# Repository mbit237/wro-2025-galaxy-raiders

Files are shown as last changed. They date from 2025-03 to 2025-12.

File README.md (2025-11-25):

# wro-2025-galaxy-raiders -- solution summary

This repository contains the full stack for the robot: electronics (PCB design and fabrication artifacts), sensors (2D LiDAR, gyro, wheel encoders, compass), decision logic (landmark-based localisation and odometry that are fused using a complementary filter), navigation (path planning, proportional steering), colour detection for the Obstacle Challenge (Raspberry Pi Camera–based colour blob detection for green and red), and a set of utilities for calibration, plotting, as well as testing.

It is implemented in Python and designed to run on a Raspberry Pi 4b which is the primary controller. The Pi interfaces directly with the sensors (LiDAR via serial/USB, MPU6050 gyro via I²C, wheel encoders via GPIO), and controls the navigation (continuous DC drive through a motor driver; steering via a PWM-controlled servo). The custom PCB consolidates power distribution, connectors, and signal routing. 

During the run, the program reads initial ranges to estimate the robot’s start pose, continuously merges odometry with landmark corrections, follows the active path, and stops automatically once a path-segment counter reaches the configured limit.

**PCB (wro-pcb-v2 folder)**
Contains everything needed to fabricate and assemble the controller board:
Schematic & PCB: Source files for the custom board (signal routing for power in, motor driver, servo PWM, I²C, UART/USB headers for sensors, encoder inputs).
Drill / CAM: Drill files and drill G-code for CNC milling; SVGs of the board outline and copper to be milled with LaserWeb 
Connected components
Power: Battery input (screw terminal), voltage regulator for motor driver, and servo.
Actuators: Screw terminals/headers to the motor driver output and a 3-pin servo header (GND, +5/6V BEC, PWM).
Sensors: I²C header for MPU6050; UART header for LiDAR; encoder inputs to GPIO connectors.
Tactile button input to GPIO for initialisation 

**Localisation using sensors:**
coind4: functions for current lidar, parsing in each data frame and checking the checksum 
gyro.py (mpu6050): basic functions for gyro to update heading
gyro_calibration_saver.py: saves the gyro calibration readings 
[unused] lds02rr.py: functions for previous lidar, also pareses in each data frame and checks the checksum
[unused] compass.py: functions for compass module to read its heading, not implemented in current version

**Navigation**
spike.py: functions to match to lidar points to landmarks 
estimate_pose.py: functions for odometry, which uses wheel rotation and gyro to estimate the robot's position and heading while it is running. New estimate_pose function uses vectors
drive.py: navigation functions 
step_count: receive signals from encoder to calculate number of steps after a certain period of time 
steering_p: driving servo motor with pwm signal that is derived from the direction in degrees
navigation.py: functions to augment robot’s paths and drive to the path which utilises proportional control to avoid steering off path

**Obstacle Challenge**
Using camera to identify the position of the red and green blocks to know which path to take at each decision point, ie after the turn at each corner
rpicam.py: functions for detection of red and green blobs based on HSV thresholds using opencv
rpicam_calibration.py: tool to calibrate HSV thresholds for different colours with sliders using opencv

**main.py:**
specify the variables and constants: filter ratios for spike and odometry, paths for the different challenges / scenarios 
get the initial position of the robot by checking the distance away from the walls
merging the positions derived from odometry and spike using complementary filter 
while loop that checks whether the path count has reached the limit to stop the programme automatically

**Miscellaneous / Testing**
motor wiring.avif: wiring for the encoder 
button.py: activate the code when button pressed 
Plotting using sockets
client_raspi.py: functions for the raspberry pi to send the lidar points to the computer for plotting 
server_comp.py: receive lidars points to plot, switch between cartesian or polar plot 
main_plotting.py: for debugging socket code

**Uploading and debugging code:**
set up ssh in raspberry pi
Log in using [username]@ipaddress, [password]
Upload code by typing:
scp C:\[file directory]\*.py [username]@ipaddres:/[file directory]
(*.py uploads python files only as the github repository has non-python files)

**Laser cutting/ 3D printing files:**
Onshape CAD: Chassis, brackets, camera/servo mounts, etc.
https://cad.onshape.com/documents?resourceType=resourceuserowner&nodeId=66495b1552a5e72f9db8f36a
Files named “[Date] Design": contain the updates made to the chassis of the car before the final design. They also contain designs for the Ackermann steering linkages, which ensure that the inner front wheel steers at a larger angle than the outer front wheel when the car turns
“Lidar measurements”: used for simpler visualisation of the first version of the initial_pose(), which calculates the car’s starting position and if it is on the left or right side of the map.
“Pcb spacer”: 3d designs to ensure that the pcb remains balanced and does not tip over which could potentially affect connections between the pcb and raspberrypi
“Camera mount”: 3d camera mounts which point the camera at a certain angle
“Differential plate”: helps to lower the axle of the rear wheels to match the level of the motor
“Lidar mount”: plate that secures the lidar sensor to the upper chassis of the car

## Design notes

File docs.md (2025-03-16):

## Link to cad 

https://cad.onshape.com/documents/3ca2ec0b9e09bc5d45a99a58/w/ab2eecc0f8901588086cb030/e/4ec6e617123936e262bbd737 
https://cad.onshape.com/documents/3d6ca03fc4376b9a668c9f46/w/3ca88911b6438fa4a43dc130/e/ea777a7d933b2682c87ee6d0
https://cad.onshape.com/documents/a7409451cb56b69469f4779f/w/586993536c800906a4209f08/e/c3c4745445447fb93e18b89e
https://cad.onshape.com/documents/cf16fbbc3dc92bb9178fcf88/w/9438730ad37c94650213375a/e/8a1cb02b4790dafd552727a4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 

## Link to documents

https://docs.google.com/document/d/1nRKID41UqzwXfIer4ROZ6MJ71AxaByn9RlcKkrrtdlg/edit?usp=sharing

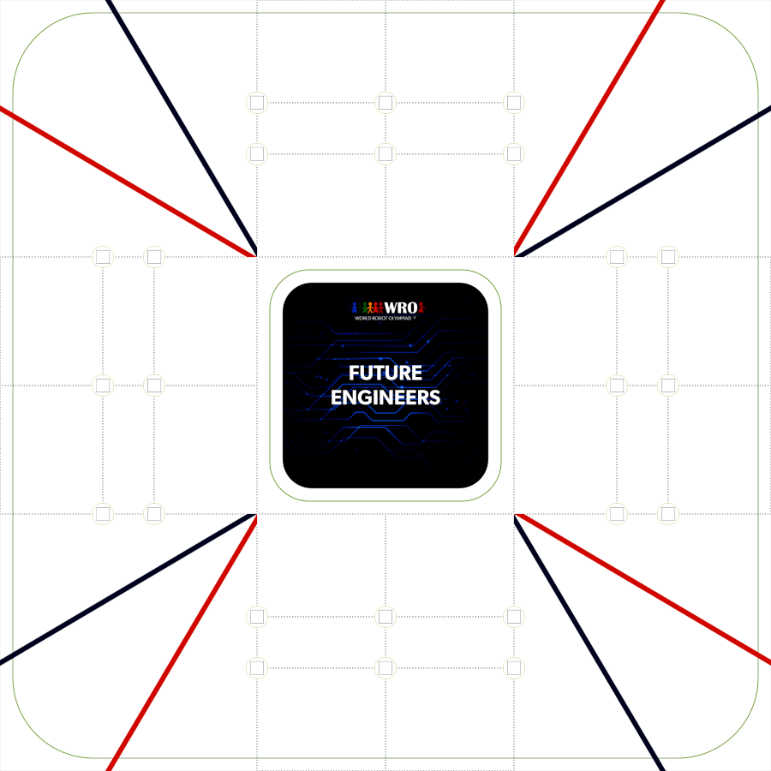
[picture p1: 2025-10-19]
FutureEngineers_Playfield_900.png

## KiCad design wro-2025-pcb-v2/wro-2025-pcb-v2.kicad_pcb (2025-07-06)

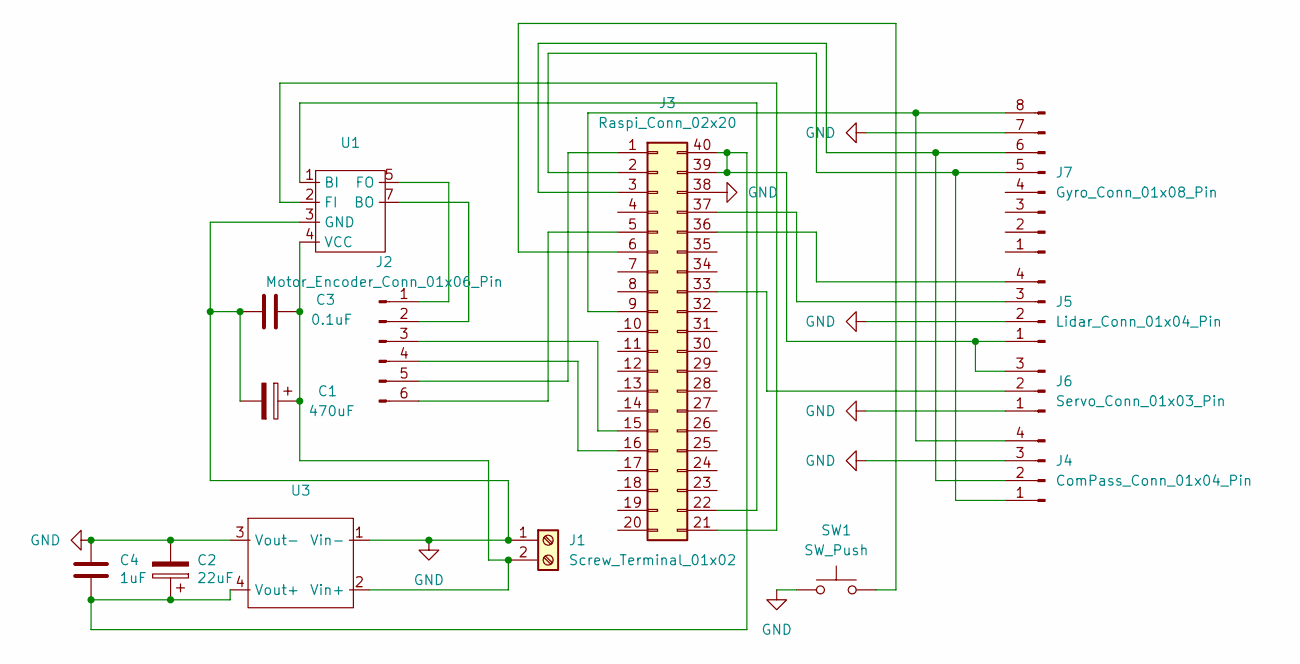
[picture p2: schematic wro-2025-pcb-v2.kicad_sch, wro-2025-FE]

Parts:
C1: 470uF; CP_Radial_D10.0mm_P5.00mm
C2: 22uF; CP_Radial_D5.0mm_P2.50mm
C3: 0.1uF; C_Disc_D4.3mm_W1.9mm_P5.00mm
C4: 1uF; C_Disc_D4.3mm_W1.9mm_P5.00mm
J1: Screw_Terminal_01x02; TerminalBlock_TE_282834-2_1x02_P5.08mm_Horizontal
J2: Motor_Encoder_Conn_01x06_Pin; PinHeader_1x06_P2.54mm_Vertical
J3: Raspi_Conn_02x20; PinHeader_2x20_P2.54mm_Vertical_SMD
J4: ComPass_Conn_01x04_Pin; PinHeader_1x04_P2.54mm_Vertical
J5: Lidar_Conn_01x04_Pin; PinHeader_1x04_P2.54mm_Vertical
J6: Servo_Conn_01x03_Pin; PinHeader_1x03_P2.54mm_Vertical
J7: Gyro_Conn_01x08_Pin; PinHeader_1x08_P2.54mm_Vertical
SW1: SW_Push; Tact_Switch_TL59AF160Q_E-Switch
U1: DIP-8_W7.62mm
U3: Voltage_Regulator_MP1584

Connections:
GND: C1.2, C2.2, C3.1, C4.1, J1.1, J3.24, J3.26, J3.31, J3.38, J4.3, J5.2, J6.1, J7.7, SW1.1, U1.3 (GND), U3.1 (Vin-), U3.3 (Vout-), U3.5, U3.7
unnamed: C1.1, C3.2, J1.2, U1.4 (VCC), U3.2 (Vin+), U3.6
unnamed: J2.1, U1.5 (FO)
unnamed: J2.2, U1.7 (BO)
unnamed: J2.3, J3.15
unnamed: J2.4, J3.16
unnamed: J2.5, J3.1
unnamed: J2.6, J3.5
unnamed: J3.2, J4.1, J7.5
unnamed: J3.3, J4.2, J7.6
unnamed: J3.6, SW1.2
unnamed: J3.9, J4.4, J7.8
unnamed: J3.21, U1.2 (FI)
unnamed: J3.22, U1.1 (BI)
unnamed: J3.33, J6.2
unnamed: J3.36, J5.4
unnamed: J3.37, J5.3
unnamed: C2.1, C4.2, J3.39, J3.40, J5.1, J6.3, U3.4 (Vout+), U3.8

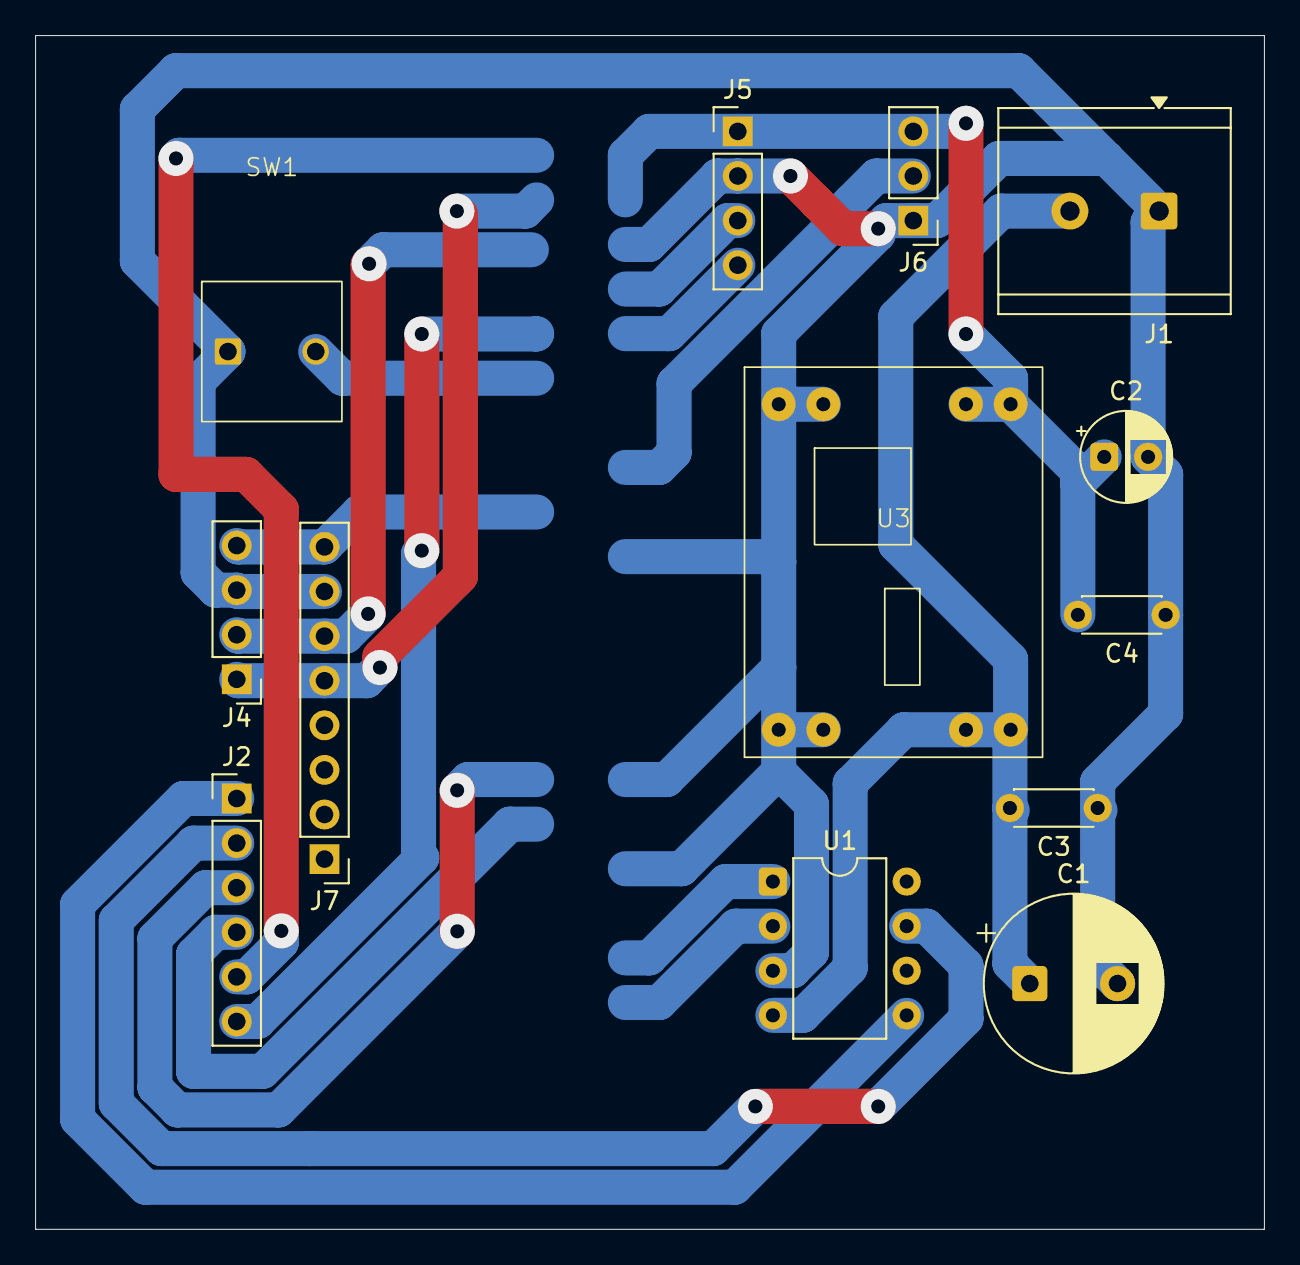
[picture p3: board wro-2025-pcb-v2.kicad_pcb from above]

Board: 2 copper layers, 70.0 x 68.0 mm, 14 parts (1 on the bottom side), 18 nets.

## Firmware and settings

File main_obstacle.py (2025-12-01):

#!/usr/bin/python
import pigpio
import time 
import struct
import math
import coind4
from gyro import Gyro
import drive
import spike
import navigation
from estimate_pose import estimate_pose, reset_pose, get_lidar_pose, lidar_update_pose
import client_raspi as client
import rpicam
from initialisation import *

POSITION_FILTER_RATIO = 0.1 
HEADING_FILTER_RATIO = 0.01  
MM_PER_STEPS = 0.296

outer_one_section = [
# straight path #1
[[200, 1000], [200, 1200]],

[[200, 1200], [200, 1350]],
# check colour
[[200, 1500], [200, 2000]], # [[200, 1500], [200, 1950]],

# turning point #1
[[200, 2000], [450, 2150.67]], # [[200, 2000], [600, 2200]],
# check colour
[[650, 2300], [650, 2346.7]], # [[700, 2400], [700, 2450]],
# check colour
]

inner_one_section = [
# straight path #1
[[800, 1000], [800, 1200]],
# check colour
[[800, 1200], [800, 1350]], 
# check colour
#turning point #1
[[800, 1400], [800, 2000]],
[[800, 2200], [850, 2200]],
[[850, 2200], [1000, 2200]], # [[850, 2200], [900, 2200]],
# check colour
]

parking_path = [[375, 1350], [375, 2000]]
ccw_parking_path = [[2400, 1600], [2900, 1800]]

unaugmented_obstacle_outer_paths, unaugmented_obstacle_inner_paths = full_path_from_one_section(outer_one_section, inner_one_section)
unaugmented_ccw_obstacle_outer_paths, unaugmented_ccw_obstacle_inner_paths = ccw_paths_from_cw(unaugmented_obstacle_outer_paths, unaugmented_obstacle_inner_paths)

unaugmented_obstacle_outer_paths[0] = [[400, 1000], [400, 1200]]
unaugmented_obstacle_outer_paths[1] = [[400, 1200], [400, 1350]]
unaugmented_obstacle_outer_paths[19] = [[700, 700], [669, 700]]
unaugmented_ccw_obstacle_outer_paths[1] = [[2600, 1200], [2600, 1350]]
unaugmented_ccw_obstacle_outer_paths[2] = [[2600, 1500], [2600, 2000]]

def exit_parking_lot():
    fwd_dist = get_distance(20)
    while fwd_dist < 500:
        # drive.steering(45)
        # drive.drive(150) # 2 seconds
        # drive.steering(-45)
        # drive.drive(-150) # 1-2 seconds
        pass
    print('no parking wall in front')
    # drive.drive(200) # until reached y:1500
    # start following path
    print('exited parking lot')
    # break

def park(ldr, pose, gyro):
    # need to add for opposite side
    global parking_path
    print("starting parking procedure")
    reverse_count = 0
    fwd_stop_y = parking_path[1][1]
    rear_stop_y = 1800
    x_min_2 = parking_path[0][0] - 15 #second alignment
    x_max_2 = parking_path[0][0] + 15 #second alignment
    x_min = x_min_2 - 15 #first alignment
    x_max = x_max_2 - 15 #first alignment
    y_min_2 = 1690 - 5
    y_max_2 = 1690 + 5
    y_min = y_min_2 - 10
    y_max = y_max_2 + 10

    print(pose)
    prev_time = time.time()
    parking_start_pos_reached = False
    
    while True:
        if reverse_count >= 4:
                rear_stop_y = parking_path[0][1]
        while pose[1] < fwd_stop_y: #forward
            pose = estimate_pose(pose, gyro.delta_z(), MM_PER_STEPS)
            navigation.drive_path(parking_path, pose, 175)
            if (time.time() - prev_time) > 0.5:
                print(pose)
                prev_time = time.time()
            if ((x_min < pose[0] < x_max) and (y_min < pose[1] < y_max) and (87 < pose[2] < 93)):
                parking_start_pos_reached = True
                break
        if parking_start_pos_reached:
            drive.drive(0)
            drive.steering(0)
            print("parking starting pos pt 1 reached")
            break    

        while pose[1] > rear_stop_y: #backward
            pose = estimate_pose(pose, gyro.delta_z(), MM_PER_STEPS)
            navigation.drive_path_back(parking_path, pose, 200)
            reverse_count += 1
            if (time.time() - prev_time) > 0.5:
                print(pose)
                prev_time = time.time()
            if ((x_min < pose[0] < x_max) and (y_min < pose[1] < y_max) and (87 < pose[2] < 93)):
                parking_start_pos_reached = True
                break
        if parking_start_pos_reached:
            drive.drive(0)
            drive.steering(0)
            print("parking starting pos pt 1 reached")
            break 

    stop_time = time.time() + 1
    while time.time() < stop_time:
        ldr.update()
    while ldr.update():
        pass
    pose = get_lidar_pose(ldr)

    print('parking starting pos pt 2')
    parking_start_pos_reached = False
    while True:
        if not ((x_min_2 < pose[0] < x_max_2) and (y_min_2 < pose[1] < y_max_2) and (87 < pose[2] < 93)):
            while pose[1] < fwd_stop_y:
                pose = lidar_update_pose(pose, gyro, ldr, MM_PER_STEPS)
                navigation.drive_path(parking_path, pose, 200)
                if (time.time() - prev_time) > 0.5:
                    print(pose)
                    prev_time = time.time()
                if ((x_min_2 < pose[0] < x_max_2) and (y_min_2 < pose[1] < y_max_2) and (87 < pose[2] < 93)):
                    parking_start_pos_reached = True
                    break
            if parking_start_pos_reached:
                drive.drive(0)
                drive.steering(0)
                print("parking starting pos pt 2 reached", pose)
                break
            while pose[1] > rear_stop_y:
                pose = lidar_update_pose(pose, gyro, ldr, MM_PER_STEPS)
                navigation.drive_path_back(parking_path, pose, 200)
                if (time.time() - prev_time) > 0.5:
                    print(pose)
                    prev_time = time.time()
                if ((x_min_2 < pose[0] < x_max_2) and (y_min_2 < pose[1] < y_max_2) and (87 < pose[2] < 93)):
                    parking_start_pos_reached = True
                    break
            if parking_start_pos_reached:
                drive.drive(0)
                drive.steering(0)
                print("parking starting pos pt 2 reached", pose)
                break 
        else:
            break

    print(get_lidar_pose(ldr))

    pose = [346.53589045596135, 1788.7217848972355, 89.71008969053936]
    print("starting to move into parking zone")
    time.sleep(3)
    # parking 
    # part 1 turn left, move back
    drive.steering(-40)
    drive.drive(-200)

    while pose[1] > 1450:
        pose = estimate_pose(pose, gyro.delta_z(), MM_PER_STEPS)

    # part 2 straight, move back
    drive.steering(0)
    drive.drive(-200)

    while pose[1] > 1425:
        pose = estimate_pose(pose, gyro.delta_z(), MM_PER_STEPS)

    # part 3 turn right, move back
    drive.steering(45)
    drive.drive(-200)

    while pose[1] > 1350:
        pose = estimate_pose(pose, gyro.delta_z(), MM_PER_STEPS)

    # part 4 turn left, move fwd 

    drive.steering(-45)
    drive.drive(0)
    start_time = time.time()
    while (time.time() - start_time) < 0.5:
        pose = estimate_pose(pose, gyro.delta_z(), MM_PER_STEPS)
    drive.drive(150)

    while pose[1] < 1400:
        pose = estimate_pose(pose, gyro.delta_z(), MM_PER_STEPS)

    drive.steering(45)
    drive.drive(0)
    start_time = time.time()
    while (time.time() - start_time) < 0.5:
        pose = estimate_pose(pose, gyro.delta_z(), MM_PER_STEPS)
    drive.drive(-150)

    while pose [1] > 1370:
        pose = estimate_pose(pose, gyro.delta_z(), MM_PER_STEPS)

    drive.steering(-45)
    drive.drive(0)
    start_time = time.time()
    while (time.time() - start_time) < 0.5:
        pose = estimate_pose(pose, gyro.delta_z(), MM_PER_STEPS)
    drive.drive(150)

    while pose[1] < 1420:
        pose = estimate_pose(pose, gyro.delta_z(), MM_PER_STEPS)

    drive.steering(0)
    drive.drive(-150)

    while pose[1] > 1380:
        pose = estimate_pose(pose, gyro.delta_z(), MM_PER_STEPS)

    drive.steering(0)
    drive.drive(0)
        
    print("parked")

def park_ccw(ldr, pose, gyro):
    global parking_path
    print(parking_path)
    print(pose[1])
    while True:
        while pose[1] < ccw_parking_path[1][1]:
            pose = estimate_pose(pose, gyro.delta_z(), MM_PER_STEPS)
            navigation.drive_path(parking_path, pose, 200)
        print("done with path")
        break
    drive.drive(0)
    drive.steering(0)

def run(gyro, ldr, pi):
    global parking_path, obstacle_inner_paths, obstacle_outer_paths, ccw_obstacle_inner_paths, ccw_obstacle_outer_paths
    # client.connect()
    while ldr.update():
        pass
    spike_pose = None
    merged_pose = None
    matches = None
    pose = initial_pose_obstacle(ldr) 
    #stop_y = pose[1] - 50 (orig)
    stop_y = 1450
    print("Initial pose:", pose)
    print("angle_z =", gyro.angle_z())
    L_dist = min(get_distance(ldr, 20), get_distance(ldr, 25), get_distance(ldr, 30), get_distance(ldr, 35), get_distance(ldr, 40), get_distance(ldr, 45))
    R_dist = min(get_distance(ldr, 340), get_distance(ldr, 335), get_distance(ldr, 330), get_distance(ldr, 325), get_distance(ldr, 320), get_distance(ldr, 315))
    path_direction = ""
    if pose[0] < 1500: #left
        obstacle_outer_paths = navigation.augment_paths(unaugmented_obstacle_inner_paths)
        obstacle_inner_paths = navigation.augment_paths(unaugmented_obstacle_outer_paths)
        parking_path = navigation.augment_path(parking_path)
        path_direction = "cw"
        print("clockwise")
    else: #right
        obstacle_inner_paths = navigation.augment_paths(unaugmented_ccw_obstacle_inner_paths)
        obstacle_outer_paths = navigation.augment_paths(unaugmented_ccw_obstacle_outer_paths)
        parking_path = navigation.augment_path(ccw_parking_path)
        path_direction = "ccw"
        print("counter-clockwise")
    paths = obstacle_inner_paths

    index = 0
    print("Paths augmented")
    path_count = 0
    print('steps', drive.steps)
    reset_pose()  
    colour = None

    reverse = False
    print("L_dist: ",  L_dist)
    if pose[0] < 1500: #left
        if R_dist < 400:
            colour = rpicam.detect_blob()
            if colour == "r":
                reverse = True
                print(colour)
                paths = obstacle_outer_paths
            else:
                print(colour)
                paths = obstacle_inner_paths
    else: #right
        if L_dist < 400:
            colour = rpicam.detect_blob()
            if colour == "g":
                reverse = True
                print(colour)
                paths = obstacle_inner_paths
            else:
                print(colour)
                paths = obstacle_outer_paths

    while reverse:
        pose = estimate_pose(pose, gyro.delta_z(), MM_PER_STEPS)
        if ldr.update():
            # print("working", time.time())
            lidar_measurements = ldr.get_measurements()
            # for l in lidar_measurements:
            #     print(l)
            # print(len(lidar_measurements))
            # break
            #spike detection
            spikes = spike.identify_spikes(lidar_measurements)
            # print(spikes)
            c_spikes = spike.add_cartesian(pose, spikes)
            # print(pose, c_spikes)
            matches = spike.match_landmarks(c_spikes)
            # client.send(matches)
            print(len(matches))
            while pose[2] > 180:
                pose[2] -= 360
            while pose[2] < -180:
                pose[2] += 360
            print(pose, matches)
            
            # if len(matches) == 0:
            #     count += 1
            #     if count > 5:
            #         drive.drive(0)
            #         time.sleep(20)
            #         count = 0
            position_error = calc_position_error(matches)
            spike_pose = calc_pose(pose, position_error)
            # print("Pose after position error:", spike_pose)
            merged_position_pose = merge_positions(pose, spike_pose, POSITION_FILTER_RATIO)
            angle_error = calc_angle_error(merged_position_pose, matches)
            # print(angle_error)
            spike_heading_pose = calc_heading(merged_position_pose, angle_error)
            # print(spike_heading_pose)
            merged_pose = merge_heading(merged_position_pose, spike_heading_pose, HEADING_FILTER_RATIO)
            # print("merged_position_pose:", merged_position_pose[2], "spike_heading_pose:", spike_heading_pose[2])
            # pose = merged_position_pose
            pose = merged_pose

        if pose[0] < 1500: #left
            drive.steer_p_back(90, pose[2], 200)
            if pose[1] <= 1100:
                break
        else: #right
            drive.steer_p_back(90, pose[2], 200)
            if pose[1] <= 1500:
                break 
    
    data_send_server = []
    while True:
        pose = estimate_pose(pose, gyro.delta_z(), MM_PER_STEPS) 
        if ldr.update():
            lidar_measurements = ldr.get_measurements()
            spikes = spike.identify_spikes(lidar_measurements)
            # print(spikes)
            c_spikes = spike.add_cartesian(pose, spikes)
            # print(pose, c_spikes)
            matches = spike.match_landmarks(c_spikes)
            # client.send(matches)

            print(len(matches))
            while pose[2] > 180:
                pose[2] -= 360
            while pose[2] < -180:
                pose[2] += 360
            print(pose, matches)

            position_error = calc_position_error(matches)
            spike_pose = calc_pose(pose, position_error)
            # print("Pose after position error:", spike_pose)
            merged_position_pose = merge_positions(pose, spike_pose, POSITION_FILTER_RATIO)
            angle_error = calc_angle_error(merged_position_pose, matches)
            # print(angle_error)
            spike_heading_pose = calc_heading(merged_position_pose, angle_error)
            # print(spike_heading_pose)
            merged_pose = merge_heading(merged_position_pose, spike_heading_pose, HEADING_FILTER_RATIO)
            # print("merged_position_pose:", merged_position_pose[2], "spike_heading_pose:", spike_heading_pose[2])
            # pose = merged_position_pose
            pose = merged_pose
            data_send_server = [spike_pose, merged_pose, matches]
            with open("troubleshootingData.txt", "w") as f:
                troubleshoot_data = str(matches) + ", " + str(merged_position_pose) + ", " + str(merged_pose)
                f.write(troubleshoot_data)
        count = navigation.drive_paths(index, paths, pose, 250)

        if count != index:
            path_count += 1
            if count % 4 == 1 and colour != None:
                print("skip check\n\n\n")
            else:
                colour = rpicam.detect_blob()
                print("colour", colour)
                if colour == 'r':
                    paths = obstacle_outer_paths
                elif colour == 'g':
                    paths = obstacle_inner_paths
            print('path', paths[count % len(paths)])

        index = count % len(paths)
        if data_send_server:
            data_send_server.append(index)
            data_send_server.append(colour)
            # client.send(data_send_server)
            data_send_server = []
        if path_count >= 60:
            if path_direction == "cw":
                if pose[1] >= stop_y:
                    print("Reached stopping pose")
                    drive.drive(0)
                    park(ldr, pose, gyro)
                    break
            elif path_direction == "ccw":
                print("parking")
                park_ccw(ldr, pose, gyro)
                print("exit function")
                break
        if pi.read(17) == 0:
            break
    print('end')

    

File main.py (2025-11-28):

#!/bin/python
import pigpio
import time 
import struct
import math 
import coind4
from gyro import Gyro 
import drive
import spike
import navigation
from estimate_pose import estimate_pose, reset_pose, get_lidar_pose, lidar_update_pose
import client_raspi as client
from initialisation import *
import main_open
import main_obstacle



navigation.PATH_GAIN = -0.5
navigation.MAX_ANGLE = 60
drive.STEER_MAX = 45
drive.CENTER = 50

pi = pigpio.pi()
pi.set_mode(17, pigpio.INPUT)
pi.set_pull_up_down(17, pigpio.PUD_UP)
print('steps', drive.steps)

ldr = coind4.CoinD4() 
ldr.start()
while ldr.update():
    pass
print("Lidar started")

gyro = Gyro()
# gyro.calibration() # keep here for now
# print("Gyro calibrated")
# pose = get_lidar_pose(ldr)
# prev_time = time.time()
# while True:
#     pose = lidar_update_pose(pose, gyro, ldr, 0.296)
#     if (time.time() - prev_time) > 0.5:
#         print(pose)
#         prev_time = time.time()

# foo()

# print("long (open)")
# gyro.calibration()
# print('gyro calibrated)')
# main_open.run(gyro, ldr, pi)

# print("short (obstacle)")
# gyro.calibration()
# print('gyro calibrated)')
# main_obstacle.run(gyro, ldr, pi)
# time.sleep(2)

while True:
    print("wait for button")
    while True:
        if pi.read(17) == 0:
            break 
    
    # button bounce
    time.sleep(0.1)

    # record time period 
    prev_time = time.time()
    while pi.read(17) == 0:
        pass
    curr_time = time.time()

    time_period = curr_time - prev_time

    # fwd_dist = get_distance(ldr, 0)
    # left_dist = get_distance(ldr, 90)
    # rear_dist = get_distance(ldr, 180)
    # right_dist = get_distance(ldr, 270)
    # print(fwd_dist, left_dist, rear_dist, right_dist)
     
    # short -- obstacle 
    if time_period < 2:
        print("short (obstacle)")
        # if gyro.load_calibration() is not None: # file not empty
        #     print("gyro calibration loaded")
        # else:
        #     gyro.calibration()
        #     gyro.save_calibration() # save new gyro calibration to file
        #     print("gyro calibrated and saved")
        gyro.calibration()
        print('gyro calibrated)')
        main_obstacle.run(gyro, ldr, pi)
        # main_open.run(gyro, ldr, pi)
        time.sleep(2)
        while ldr.update():
            pass

    # long -- open 
    # elif time_period < 6:
    #     print("long (open)")
    #     # if gyro.load_calibration() is not None: # file not empty
    #     #     print("gyro calibration loaded")
    #     # else:
    #     #     gyro.calibration()
    #     #     gyro.save_calibration() # save new gyro calibration to file
    #     #     print("gyro calibrated and saved")
    #     gyro.calibration()
    #     print('gyro calibrated)')
    #     main_open.run(gyro, ldr, pi)
    #     time.sleep(2)
    #     while ldr.update():
    #         pass
    # # long long -- calibrate gyro 
    # else:
    #     print("long long (gyro)")
    #     # time.sleep(1)
    #     # if gyro.load_calibration() is not None: # file not empty
    #     #     print("gyro calibration loaded")
    #     # else:
    #     gyro.calibration()
    #     gyro.save_calibration() # save new gyro calibration to file
    #     print("gyro calibrated and saved")
    #     while ldr.update():
    #         pass

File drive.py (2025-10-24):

import pigpio

STEER_MAX = 45
CENTER = 45

#GPIO20, GPIO21

pi = pigpio.pi()
pi.set_PWM_frequency(20, 200)

def drive(speed): # 0-255
    if speed > 0:
        pi.set_PWM_dutycycle(20, 255-speed)
        pi.set_PWM_dutycycle(21, 255)
    else:
        pi.set_PWM_dutycycle(20, 255)
        pi.set_PWM_dutycycle(21, 255+speed)

def steering(dir):
    if dir < -STEER_MAX:
        dir = -STEER_MAX
    elif dir > STEER_MAX:
        dir = STEER_MAX
    pulse_duration = 1340 + (80 / 9) *(dir + CENTER) - 400
    pi.set_servo_pulsewidth(23, pulse_duration)

steps = 0
pin6_level = False
# gpio -- pin 
# level -- rising / falling edge 
# tick -- The number of microseconds since boot
def step_count(gpio, level, tick):
    global steps
    if pin6_level:
        steps += 1
    else:
        steps -= 1
    # steps += 1

def drive_dir(gpio, level, tick):
    global pin6_level 
    if level == 1:
        pin6_level = True 
    elif level == 0:
        pin6_level = False 

def steer_p(dir, curr_angle, speed):
    while curr_angle - dir > 180:
        curr_angle -= 360
    while curr_angle - dir < -180:
        curr_angle += 360

    error = curr_angle - dir
    gain = 2 
    correction = error * gain 
    steering(correction)
    drive(speed)

def steer_p_back(dir, curr_angle, speed):
    while curr_angle - dir > 180:
        curr_angle -= 360
    while curr_angle - dir < -180:
        curr_angle += 360

    error = curr_angle - dir
    gain = -2 
    correction = error * gain 
    steering(correction)
    drive(-speed) 

cb1 = pi.callback(5, pigpio.RISING_EDGE, step_count)
cb2 = pi.callback(6, pigpio.EITHER_EDGE, drive_dir)

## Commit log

2025-03-16 Add motor-withencoder-wiring-file.avif
2025-04-13 added gyro using smbus
2025-04-27 add steering function
2025-05-04 added lidar but could not read successfully
2025-05-11 finished lidar
2025-05-18 removed pi argument from lidar
2025-05-18 add new lidar coind4
2025-05-25 testing motor
2025-06-01 added socket programme
2025-06-01 camera calibration for webcam and raspberrypi
2025-06-01 plotting lidar (failed)
2025-06-03 Fixed plotting of lidar points
    [client_raspi.py, server_comp.py]
2025-06-08 added spike.py for spike detection, removed uart arg in CoinD4 __init__,
2025-06-08 added gyro calibration save
2025-06-13 added code to estimate pose of robot, changed gyro calibration time to 10 secs, duplicated main code to test gyro calibration
2025-06-13 Plot matches on a cartesian plane using socket
2025-06-15 minor fixes in estimate pose
    [estimate_pose.py, main.py]
2025-06-22 changed initial pose function to deduce side from detected spikes + added print x and y position
2025-06-29 changed pulse_duration in drive.py, minor fix in estimate_pose.py and gyro.py, minor fixes in main, tuned PATH_GAIN, added stop.py
    [drive.py, estimate_pose.py, main.py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]
2025-07-06 added merge_position and merge_heading to reduce drifting
    [main.py, navigation.py, spike.py]
2025-07-06 Add PCB files
    [wro-2025-pcb-v2.kicad_pcb, wro-2025-pcb-v2.kicad_sch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]
2025-07-13 tweaked POSITION_FILTER_RATIO and HEADING_FILTER_RATIO to ensure that robot does not drift too far from the path, added difference in c_spike x, y and landmark x, y in match_landmarks for debugging
    [main.py, spike.py]
2025-07-27 fixed estimate_pose, tweaked filter ratio
    [estimate_pose.py, main.py]
2025-08-10 update plotting of lidar
2025-08-10 gyro + navigation testing
2025-08-17 button code
2025-08-17 fixed inner and outer paths for obstacle challenge
    [main.py]
2025-08-24 Fixed gyro calibration and added stop
    [estimate_pose.py, main.py]
2025-08-31 camera cropping
2025-09-05 print statement to print colour detected for obstacle challenge
2025-09-05 commented unnecessary prints
2025-09-09 Updated button programme
2025-09-09 button stop for open challenge
2025-10-12 added program to test lidar
2025-10-12 minor changes to lidar test code
2025-11-21 changed max steer angle to 60
2025-11-22 fixed getting into parking position with lidar
    [estimate_pose.py, initialisation.py, main.py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]
2025-11-24 MOSTLY WORKING CAN USE FOR FINALS, PLS REVERT TO THIS IF ANYTHING ELSE IN THE FUTURE FAILS
    [drive.py, main.py, main_open.py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]
2025-11-24 STILL WORKING BUT WITH MINOR CHANGES TO FIX CERTAIN OBSTACLE SCENARIOS
    [main_obstacle.py]
2025-11-25 fixed socket disconnect
2025-11-25 changes to flip direction when avoiding red and green obstacles. CORRECT VERSION
    [client_raspi.py, main_obstacle.py]
2025-11-25 reverted back to button presses to start robot run
    [main.py]
